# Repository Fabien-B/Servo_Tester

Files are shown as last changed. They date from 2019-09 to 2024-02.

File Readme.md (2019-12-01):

Servo Tester
=============

_This project is a work in progress. Some features are missing._

A device to quickly command servomoteurs and other stuff like I2C or CAN devices.

Based on a nucleo32 L432KC, this device allow to command up to 5 (only 3 working for now) classic servomotors.
It also support dynamixel AX-12A servomotors.

## Hardware

PCB was made with Kicad 5.0. Go to the Release page to get the gerbers files.

Run `git submodule update --init --recursive` to fetch kicad libraries.

## Software

The embedded firware uses ChibiOs.

For instructions about embedded firmware go to the appropriate [Readme file](software/embedded/Readme.md).

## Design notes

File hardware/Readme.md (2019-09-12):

Tester hardware
================

The jumpers configuration on the NUCLEO L432KC needs to be changed: remove SB18, SB16 (for the I2C) and SB9 (to allow powering through 5V pin).

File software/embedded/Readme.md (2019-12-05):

Testeur software
================

To build the firmware, there is few thing you need to have.

First, Fetch ChibiOs and some third party contributions with `git submodule update --init --recursive`.

__Install Perl dependencies (used to generate board.h file from board.cfg):__

```
sudo apt update
sudo apt install libc6:i386 libncurses5:i386 libstdc++6:i386
sudo apt install libmodern-perl-perl libxml-libxml-perl
sudo perl -MCPAN -e 'install String::LCSS'
```

__Install GCC for ARM:__

Fetch the latest version from [https://developer.arm.com/open-source/gnu-toolchain/gnu-rm/downloads](https://developer.arm.com/open-source/gnu-toolchain/gnu-rm/downloads).

Extract it to `/usr/local` (or anywhere you want).

Make a symbolic link to it (adapt the command with the right version name):

```
cd /usr/local
ln -s  gcc-arm-none-eabi-7-2017-q4-major gcc-arm-none-eabi
```

Add it to your $PATH by adding this line either in your ~/.profile or ~./bashrc:

`PATH="$PATH:/usr/local/gcc-arm-none-eabi/bin"`

__Install STM32CubeMX__

Download and install SMT32CubeMx with admin rights (need to signup on st.com): [http://www.st.com/en/development-tools/stm32cubemx.html](http://www.st.com/en/development-tools/stm32cubemx.html).

Make sure it is installed in `/usr/local` for linux users (_not_ in your $HOME) or `C:\Program Files` for windows users.

__Edit udev rules for Black Magic Probe__

If you are using the nucleo with black magic probe, install the udev rule :

`sudo cp 49-black_magic_probe.rules /etc/udev/rules.d/`

and update them with :

`sudo udevadm control --reload-rules && sudo udevadm trigger`

__Build__

To build the firmware, go to software/embedded then run `make`.

To flash the firmware, copy paste the .bin generated file to your nucleo.

If your nucleo StLink has been flashed with [BlackMagicProbe](https://github.com/blacksphere/blackmagic/), run `make flash`.

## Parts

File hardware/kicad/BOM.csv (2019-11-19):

Id | Référence | Boîtier | Quantité | Désignation | Fournisseur et réf | prix unitaire | total quantité
1 | S1,S2,S3,S4,S5 | PinHeader_1x03_P2.54mm_Vertical | 5 | JServo | Usual 2.54mm pin header | 0,1 | 0,5
2 | I2C1_a1,I2C1_b1,CAN1 | PinHeader_1x04_P2.54mm_Vertical | 3 | J_01x04P2.54 | Usual 2.54mm pin header | 0,1 | 0,3
3 | DYN1,DYN2 | SHDR3W70P0X250_1X3_990X490X590P | 2 | 22-03-5035 | https://fr.rs-online.com/web/p/embases-circuits-imprimes/6878048P/ | 0,388 | 0,776
4 | C1,C4 | C_0603_1608Metric | 2 | 100nF |  | 0,1 | 0,2
5 | C3,C5 | C_0603_1608Metric | 2 | 330nF |  | 0,1 | 0,2
6 | C2 | CP_EIA-7343-31_Kemet-D | 1 | 100µF | https://fr.rs-online.com/web/p/condensateurs-tantale/6480402/ | 0,403 | 0,403
7 | R1 | R_0603_1608Metric | 1 | 120Ω |  | 0,1 | 0,1
8 | R2,R3 | R_0603_1608Metric | 2 | 390Ω |  | 0,1 | 0,2
9 | R4,R9,R10 | R_0603_1608Metric | 3 | 10k |  | 0,1 | 0,3
10 | R5,R7,R8 | R_0603_1608Metric | 3 | 2.2k |  | 0,1 | 0,3
11 | R6 | R_0603_1608Metric | 1 | 1k |  | 0,1 | 0,1
12 | RV1 | TS53YL | 1 | R_POT | https://fr.rs-online.com/web/p/trimmers/4867526/ | 1,258 | 1,258
13 | D1,D2 | LED_0603_1608Metric | 2 | LED |  | 0,1 | 0,2
14 | DS1 | WC1602A | 1 | WC1602A | Standard LCD 16x2 | 6 | 6
15 | Ret1 | SW_PUSH_6mm_H5mm | 1 | Push_Switch | Dummy push switch | 0,1 | 0,1
16 | OK1 | RotaryEncoder_Alps_EC11E-Switch_Vertical_H20mm | 1 | Rotary_Encoder_Switch | https://fr.rs-online.com/web/p/encodeurs-rotatifs-mecaniques/7295589/ | 4,08 | 4,08
17 | U1 | TSR-2 | 1 | TSR_2-2450 | https://fr.rs-online.com/web/p/regulateurs-a-decoupage/9068487/ | 13,1 | 13,1
18 | U2 | SOIC-8_3.9x4.9mm_P1.27mm | 1 | MCP2551-I-SN | https://fr.rs-online.com/web/p/transceivers-can/7386036/ | 1,122 | 1,122
19 | U3 | NUCLEO32 | 1 | NUCLEO32-L432KC | https://fr.rs-online.com/web/p/kits-de-developpement-pour-processeurs-et-microcontroleurs/1438574/ | 11,36 | 11,36
20 | U4 | SOP-16_7.5x10.4mm_P1.27mm | 1 | PCA9554D | https://fr.rs-online.com/web/p/expandeurs-e-s/4837171/ | 1,63 | 1,63
 |  |  |  |  |  |  | Total
 |  |  |  |  |  |  | 42,229

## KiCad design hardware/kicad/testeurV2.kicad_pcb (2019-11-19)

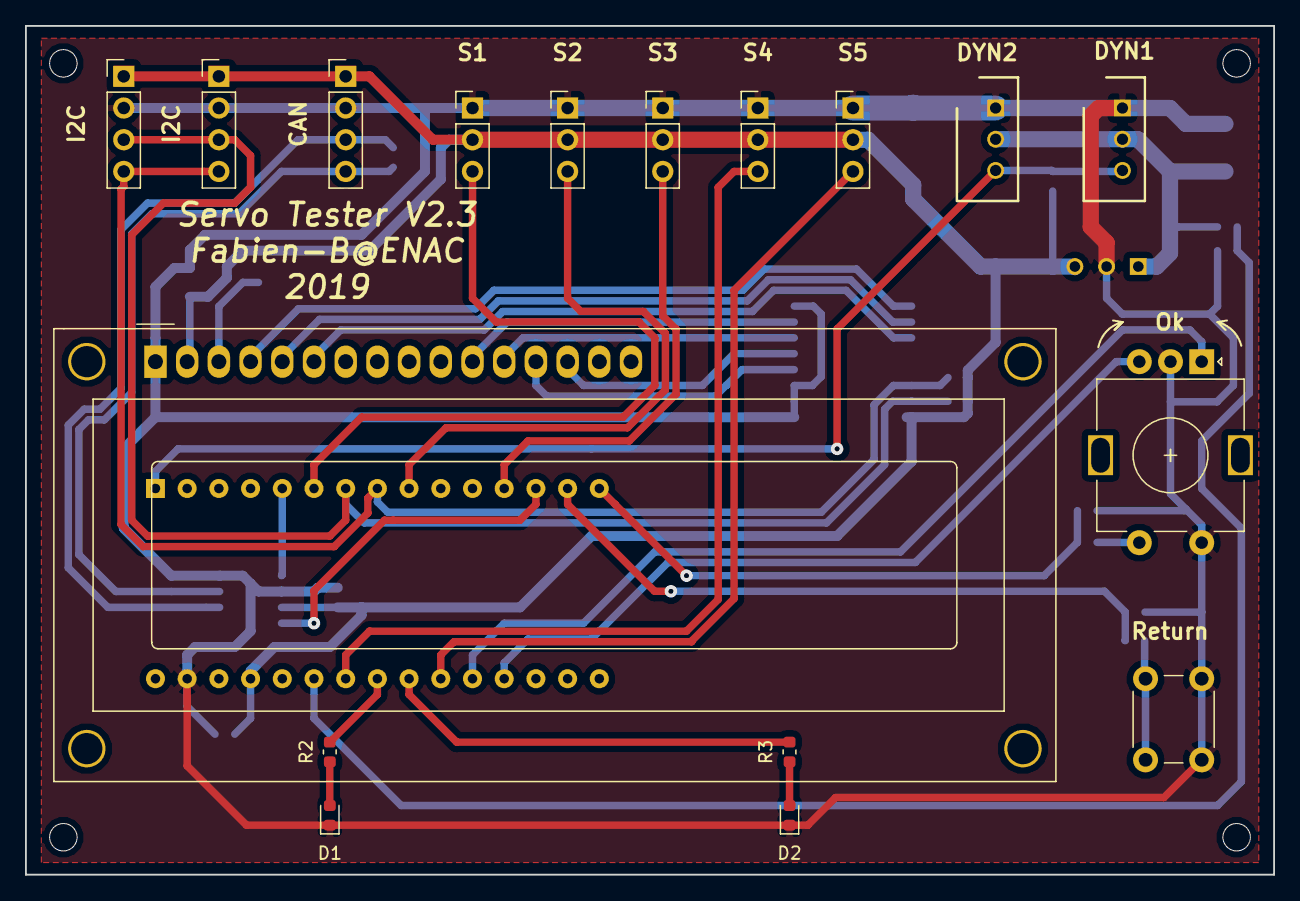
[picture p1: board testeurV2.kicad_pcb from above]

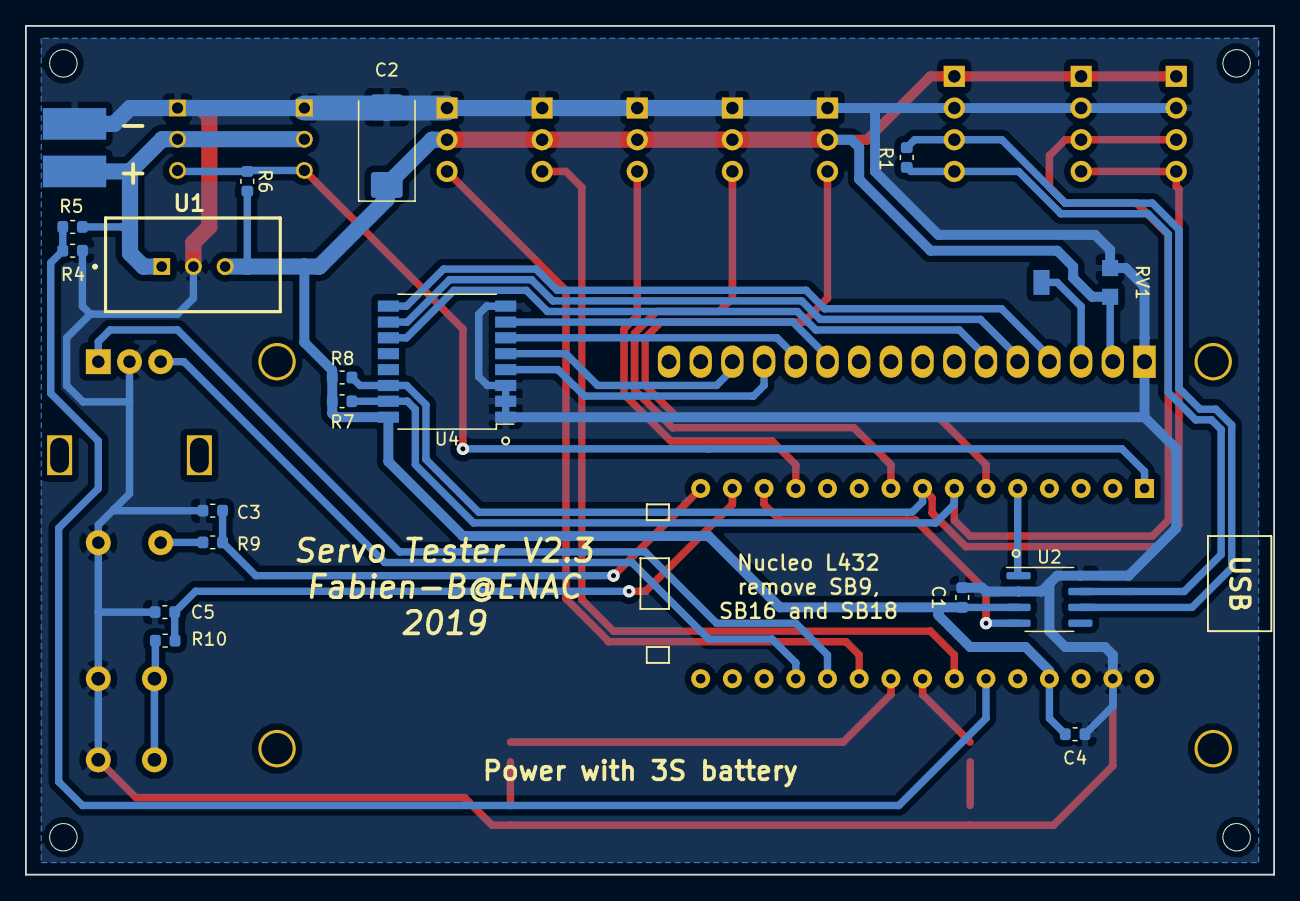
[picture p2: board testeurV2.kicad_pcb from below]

Board: 2 copper layers, 100.0 x 68.0 mm, 36 parts (19 on the bottom side), 34 nets.

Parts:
C1, C4: 100nF; C_0603_1608Metric
C2: 100µF; CP_EIA-7343-31_Kemet-D
C3, C5: 330nF; C_0603_1608Metric
CAN1: J_01x04P2.54; PinHeader_1x04_P2.54mm_Vertical
D1, D2: LED; LED_0603_1608Metric
DS1: WC1602A
DYN1, DYN2: 22-03-5035; SHDR3W70P0X250_1X3_990X490X590P
I2C1_a1, I2C1_b1: J_01x04P2.54; PinHeader_1x04_P2.54mm_Vertical
OK1: Rotary_Encoder_Switch; RotaryEncoder_Alps_EC11E-Switch_Vertical_H20mm
P1: Power_pads
R1: 120Ω; R_0603_1608Metric
R2, R3: 390Ω; R_0603_1608Metric
R4, R9, R10: 10k; R_0603_1608Metric
R5, R7, R8: 2.2k; R_0603_1608Metric
R6: 1k; R_0603_1608Metric
RV1: R_POT; TS53YL
Ret1: Push_Switch; SW_PUSH_6mm_H5mm
S1, S2, S3, S4, S5: JServo; PinHeader_1x03_P2.54mm_Vertical
U1: TSR_2-2450; TSR-2
U2: MCP2551-I-SN; SOIC-8_3.9x4.9mm_P1.27mm
U3: NUCLEO32-L432KC; NUCLEO32
U4: PCA9554D; SOP-16_7.5x10.4mm_P1.27mm

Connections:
+5V: C1.2, C2.1, C4.2, CAN1.1, DS1.2, I2C1_a1.1, I2C1_b1.1, R6.2, R7.1, R8.1, RV1.3, S1.2, S2.2, S3.2, S4.2, S5.2, U1.3, U2.3, U3.27, U4.16
+12V: DYN1.2, DYN2.2, P1.2, R4.1, U1.1
/BAT_MEAS: R4.2, R5.1, U3.25
/CAN_RX: U2.4, U3.13
/CAN_TX: U2.1, U3.5
/DYNAMIXEL: DYN1.3, DYN2.3, R6.1, U3.1
/ENC_A: OK1.A, U3.20
/ENC_B: OK1.B, U3.19
/I2C1_SCL: I2C1_a1.4, I2C1_b1.4, R8.2, U3.8, U4.14
/I2C1_SDA: I2C1_a1.3, I2C1_b1.3, R7.2, U3.7, U4.15
/OK_BTN: C3.1, R9.1, U3.15
/RET_BTN: C5.1, R10.1, U3.14
/SERVO1: S1.3, U3.6
/SERVO2: S2.3, U3.9
/SERVO3: S3.3, U3.12
/SERVO4: S4.3, U3.24
/SERVO5: S5.3, U3.21
GND: C1.1, C2.2, C3.2, C4.1, C5.2, CAN1.2, D1.1, D2.1, DS1.1, DYN1.1, DYN2.1, I2C1_a1.2, I2C1_b1.2, OK1.C, OK1.S2, P1.1, R5.2, RV1.1, Ret1.1, S1.1, S2.1, S3.1, S4.1, S5.1, U1.2, U2.2, U2.8, U3.29, U4.1, U4.2, U4.3, U4.8
unnamed: CAN1.3, R1.2, U2.6
unnamed: CAN1.4, R1.1, U2.7
unnamed: D1.2, R2.1
unnamed: D2.2, R3.1
unnamed: DS1.3, RV1.2
unnamed: DS1.4, U4.9
unnamed: DS1.5, U4.10
unnamed: DS1.6, U4.11
unnamed: DS1.11, U4.7
unnamed: DS1.12, U4.6
unnamed: DS1.13, U4.4
unnamed: DS1.14, U4.5
unnamed: OK1.S1, R9.2
unnamed: R2.2, U3.23
unnamed: R3.2, U3.22
unnamed: R10.2, Ret1.2

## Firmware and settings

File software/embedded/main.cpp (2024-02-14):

extern "C" {

#include "globalVar.h"
#include "stdutil.h"
#include "lcd.h"
#include "servos.h"
}
#include <ch.h>
#include <hal.h>

#include "hardware_config.h"
#include "ttyConsole.h"
#include "ui.h"
#include "StateMachine/StateManager.h"


static THD_WORKING_AREA(waUiStateMachine, 500);

StateManager stateManager = StateManager();
static void runStateMachine (void *arg)
{
  (void)arg;
  chRegSetThreadName("uiStateMachine");
  stateManager.run();
}


int main(void) {
  /*
   * System initializations.
   * - HAL initialization, this also initializes the configured device drivers
   *   and performs the board-specific initializations.
   * - Kernel initialization, the main() function becomes a thread and the
   *   RTOS is active.
   */
  halInit();
  chSysInit();
  initHeap();

  init_servos();
  init_I2C();
  init_ui();

  stateManager.init();

  chThdCreateStatic(waUiStateMachine, sizeof(waUiStateMachine), NORMALPRIO, &runStateMachine, NULL);

  consoleInit(); // initialisation de la liaison série du shell
  consoleLaunch();  // lancement du thread qui gère le shell sur la liaison série


  // main thread does nothing
  chThdSleep(TIME_INFINITE);
}

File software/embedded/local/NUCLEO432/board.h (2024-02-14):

/*
    ChibiOS - Copyright (C) 2006..2015 Giovanni Di Sirio

    Licensed under the Apache License, Version 2.0 (the "License");
    you may not use this file except in compliance with the License.
    You may obtain a copy of the License at

        http://www.apache.org/licenses/LICENSE-2.0

    Unless required by applicable law or agreed to in writing, software
    distributed under the License is distributed on an "AS IS" BASIS,
    WITHOUT WARRANTIES OR CONDITIONS OF ANY KIND, either express or implied.
    See the License for the specific language governing permissions and
    limitations under the License.
*/

#pragma once


/*
 * Setup for STMicroelectronics STM32 Nucleo32-L432KC board.
 */

/*
 * Board identifier.
 */
#define BOARD_ST_NUCLEO32_L432KC
#define BOARD_NAME                  "STMicroelectronics STM32 Nucleo32-L432KC"

/*
 * Board oscillators-related settings.
 * NOTE: HSE not fitted.
 */
#if !defined(STM32_LSECLK)
#define STM32_LSECLK                32768U
#endif

#define STM32_LSEDRV                (2U << 3U)

#if !defined(STM32_HSECLK)
#define STM32_HSECLK                0U
#endif

/*
 * Board voltages.
 * Required for performance limits calculation.
 */
#define STM32_VDD                   300U

/*
 * MCU type as defined in the ST header.
 */
#define STM32L432xx

/*
 * IO pins assignments.
 */
/*
 * IO pins assignments.
 */
#define	ENC_A                          0U
#define	ENC_B                          1U
#define	VCP_TX                         2U
#define	SERVO5                         3U
#define	LED1                           4U
#define	LED2                           5U
#define	SERVO4                         6U
#define	BAT_MEAS                       7U
#define	SERVO3                         8U
#define	TERMINAL_TX                    9U
#define	PA10                           10U
#define	CAN_RX                         11U
#define	CAN_TX                         12U
#define	SWDIO                          13U
#define	SWCLK                          14U
#define	VCP_RX                         15U

#define	SERVO1                         0U
#define	SERVO2                         1U
#define	PB02                           2U
#define	LED_GREEN                      3U
#define	OK_BTN                         4U
#define	RET_BTN                        5U
#define	SCL                            6U
#define	SDA                            7U
#define	PB08                           8U
#define	PB09                           9U
#define	PB10                           10U
#define	PB11                           11U
#define	PB12                           12U
#define	PB13                           13U
#define	PB14                           14U
#define	PB15                           15U

#define	PC00                           0U
#define	PC01                           1U
#define	PC02                           2U
#define	PC03                           3U
#define	PC04                           4U
#define	PC05                           5U
#define	PC06                           6U
#define	PC07                           7U
#define	PC08                           8U
#define	PC09                           9U
#define	PC10                           10U
#define	PC11                           11U
#define	PC12                           12U
#define	PC13                           13U
#define	PC14                           14U
#define	PC15                           15U

#define	PD00                           0U
#define	PD01                           1U
#define	PD02                           2U
#define	PD03                           3U
#define	PD04                           4U
#define	PD05                           5U
#define	PD06                           6U
#define	PD07                           7U
#define	PD08                           8U
#define	PD09                           9U
#define	PD10                           10U
#define	PD11                           11U
#define	PD12                           12U
#define	PD13                           13U
#define	PD14                           14U
#define	PD15                           15U

#define	PH00                           0U
#define	PH01                           1U
#define	PH02                           2U
#define	PH03                           3U
#define	PH04                           4U
#define	PH05                           5U
#define	PH06                           6U
#define	PH07                           7U
#define	PH08                           8U
#define	PH09                           9U
#define	PH10                           10U
#define	PH11                           11U
#define	PH12                           12U
#define	PH13                           13U
#define	PH14                           14U
#define	PH15                           15U
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

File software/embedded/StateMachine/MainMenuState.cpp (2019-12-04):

//
// Created by fabien on 10/10/2019.
//

#include "MainMenuState.h"
#include "lcd.h"
#include "stdio.h"
#include "stdutil.h"
#include "servos.h"
#include "ServoState.h"
#include "DynamixelState.h"
#include "I2CState.h"

MainMenuState mainMenuState = MainMenuState();

char* titles_mainmenu[] = {
	(char*)"Servos    ",
	(char*)"Dynamixels",
	(char*)"I2C       ",
	(char*)"CAN       "
};

void MainMenuState::enter(int32_t pos_enc) {
	pos_enc_init = pos_enc;
    char title[] = "                ";
	lcdWriteString(&LCDD1, title, 0);
	lcdWriteString(&LCDD1, titles_mainmenu[0], 0);
	char blank[] = "                ";
	lcdWriteString(&LCDD1, blank, 40);
}

void MainMenuState::leave() {
    
}

AbstractState* MainMenuState::onUiEvent(struct UiState ui_state) {
	int i = (ui_state.pos_enc - pos_enc_init) % (sizeof(titles_mainmenu)/sizeof(*titles_mainmenu));
	
	if(ui_state.enc_changed) {	
		lcdWriteString(&LCDD1, titles_mainmenu[i], 0);
	}

	if(ui_state.ok_clicked) {
		switch (i) {
		case 0:
			return &servoState;
			break;
		case 1:
			return &dynamixelIDState;
			break;
		case 2:
			return &i2cState;
			break;
		default:
			return nullptr;
			break;
		}
	}

	return nullptr;
}

AbstractState* MainMenuState::periodic() {
    return nullptr;
}

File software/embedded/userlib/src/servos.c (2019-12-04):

/*
 * servos.c
 *
 *  Created on: 18 juin 2019
 *      Author: fabien
 */

#include "servos.h"
#include <ch.h>
#include <hal.h>
#include "globalVar.h"
#include "stdutil.h"

PWMConfig pwmcfg1 = {
	.frequency = 1000000,
	.period = 20000,
	.callback = NULL,
	.channels = {
			{								//ch1
					.mode = PWM_OUTPUT_ACTIVE_HIGH,
					.callback = NULL
			},
			{								//ch2n
					.mode = PWM_COMPLEMENTARY_OUTPUT_ACTIVE_HIGH,
					.callback = NULL
			},
			{								//ch3n
					.mode = PWM_COMPLEMENTARY_OUTPUT_ACTIVE_HIGH,
					.callback = NULL
			},
			{PWM_OUTPUT_DISABLED, NULL}
	},
	.cr2 = 0,
	.bdtr = 0,
	.dier = 0
};

// PWMConfig pwmcfg16 = {
// 	.frequency = 1000000,
// 	.period = 20000,
// 	.callback = NULL,
// 	.channels = {
// 			{								//ch1
// 					.mode = PWM_OUTPUT_ACTIVE_HIGH,
// 					.callback = NULL
// 			},
// 			{PWM_OUTPUT_DISABLED, NULL},	//ch2
// 			{PWM_OUTPUT_DISABLED, NULL},	//ch3
// 			{PWM_OUTPUT_DISABLED, NULL}		//ch4
// 	},
// 	.cr2 = 0,
// 	.bdtr = 0,
// 	.dier = 0
// };

PWMDriver* _servo_drivers[5] = {
		&PWMD1, &PWMD1, &PWMD1,
		NULL,	//&PWMD16,		TODO fix issue with TIM16 !!!
		NULL, //&PWMD2
};

int _servo_channels[5] = {
		1, 2, 0, 0, 3
};

void init_servos() {
	pwmStart(&PWMD1, &pwmcfg1);
	//pwmStart(&PWMD2, &pwmcfg2);
	//pwmStart(&PWMD16, &pwmcfg16);

}

void enable_servos() {
	  for(int i=0; i<5; i++) {
		  set_servo(i, 1000);
	  }
}

void set_servo(int servo_nb, int us) {
	if (servo_nb < 1 || servo_nb > 3) {	// TODO FixMe: only works for TIM1 for now, ie first 3 servos.
		return;
	}
	servo_nb -= 1;
	us = CLAMP_TO(100, 3000, us);
	pwmEnableChannel(_servo_drivers[servo_nb], _servo_channels[servo_nb], us);
}

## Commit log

2019-06-14 Adds schematics.
    [testeurV2.sch]
2019-06-16 Assigns footprints.
    [testeurV2.sch]
2019-06-16 convenience edits.
    [testeurV2.sch]
2019-06-16 components placing.
    [testeurV2.kicad_pcb]
2019-06-17 testeurV2 R0.1
    [testeurV2.kicad_pcb, testeurV2.sch]
2019-06-19 Adds pullup for dynamixels.
    [testeurV2.kicad_pcb, testeurV2.sch]
2019-09-12 Adds MAX6818 to debounce buttons. Adds missing pullup on dynamixel UART.
    [testeurV2.kicad_pcb, testeurV2.sch]
2019-09-12 Change directory tree. Adds I2C pullups.
    [testeurV2.kicad_pcb, testeurV2.sch]
2019-09-16 Adds 2nd board version.
    [testeurV2.sch, testeurV2_JLCPCB.kicad_pcb]
2019-10-11 [1st Firmware] Adds first firmware version. Features servo moves, Dynamixel move, setId, endless mode.
    [board.cfg]
2019-10-11 [Harware] Update to last version.
    [testeurV2_JLCPCB.kicad_pcb]
2019-10-29 Fix hardware and move to V2.3.
    [testeurV2.sch, testeurV2_JLCPCB.kicad_pcb]
2019-11-19 Rename file + change some part names.
    [testeurV2.kicad_pcb, testeurV2.sch, testeurV2_JLCPCB.kicad_pcb]
2019-11-19 Adds component cost estimation.
    [BOM.csv]
2019-11-19 Removes old file and rename kicad files.
    [testeurV2.kicad_pcb]
2019-12-03 Uses hardware encoders.
    [board.cfg]
2019-12-03 Adds udev rule for black magic probe.
2019-12-03 Add instructions about udev rules for black magic probe.
2019-12-04 Add SRF02 driver.
2019-12-05 Adds VL6180x driver.
2019-12-05 Adds missing dependencies and fix typo.
    [I2CState.cpp]
2023-06-20 Set Dynamixel TX as push-pull. In half-duplex, TX is push-pull during a transaction, and Hi-Z otherwise.
    [board.cfg]
